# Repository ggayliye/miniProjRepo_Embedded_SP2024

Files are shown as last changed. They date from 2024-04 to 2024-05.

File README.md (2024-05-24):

# Project: Water Storage Tank Refill And Safety Control

Authors: Kyle G. Gayliyev, Hazen R. Brown, Prasanna Umbarkar, Mihir Rane <br>
Date: 29- March - 2024<br>
Course: ECE 6780 - Embedded System Design, ECE Department, The University of Utah<br>
GitHub IDs: ggayliye, Hrb2003, prasannaumbarkar09, patientcoderMR7 <br>
Repo: https://github.com/ggayliye/miniProjRepo_Embedded_SP2024 <br>
Date: By 26-April-2024, 11:59pm (Time of when submission is due/will be ready to be evaluated)<br>
Copyright: ECE 6780, Kyle G. Gayliyev  - This work may not be copied for use in Academic Coursework.

## Overview of the Project
* Pumping water into a container that stops by itself when it's full and fills back again the exact amount when it gets empty. 
* Water fill station that automatically stops dispensing when full, implementation would sense water level without touching it. 
* A small 4V water pump will be connected to the power. The objective is to refill a water container. Once it reaches its high/full level, a signal will be sent to the microcontroller. The microcontroller will interrupt the water pump indicating the water container is full. The same process will take place when it’s empty. The water pump will start working and pump water into the container. 
* The container will include a sensor. This sensor will be placed on the bottom of the container. It’ll sense when the container is “empty” and ready to be refilled. To determine the container’s full state, the water-amount-calculation method will be used: the volume of the container will be known (mL), the speed of the pump for flowing water through a vinyl pipe will be known (x mL/s), and we calculate the amount of time the water pump should be kept on. 
* For the water safety control circuit, we use a MOSFET, an op-amp, an LED, and a speaker. When the water gets salty (adding salt to the water), the alarm will sound along with an LED warning the water is not safe.
* Once the water starts filling the tank, a message is popped on the terminal "Tank empty-water filling in progress" and when completed "tank filled". Also when salt is added toxicity of water can be indicated by "toxic water" on the terminal. This is all done by UART.
* The water safety implementation will only be based on chemicals that are ionic and/or electroconductive. Specifically, we will focus on Sodium chloride (NaCl) in our testing. This means that the “unsafe” measurement will be sensitive to salt. 
* The technical implementation of the “unsafe water” indicator is going to be in the container. It’s planned to be a simple design: installing an active power probs inside the container. When water hosts polluting electroconductive elements, it will create a path to transfer electrons that will trigger the measuring sensor. The power source will be set very low; it will be very safe to use. 
* This project has applications in drinking water storage tanks, petroleum refineries, and more. 
* Our design will be very safe to use as we take all precautions and safety measurements before the launch.
* In this project, we implemented interrupt, GPIO, UART, and motor drive.
* For the software, we used C programming language and coded using Keil uVision5.

## List of Materials : 

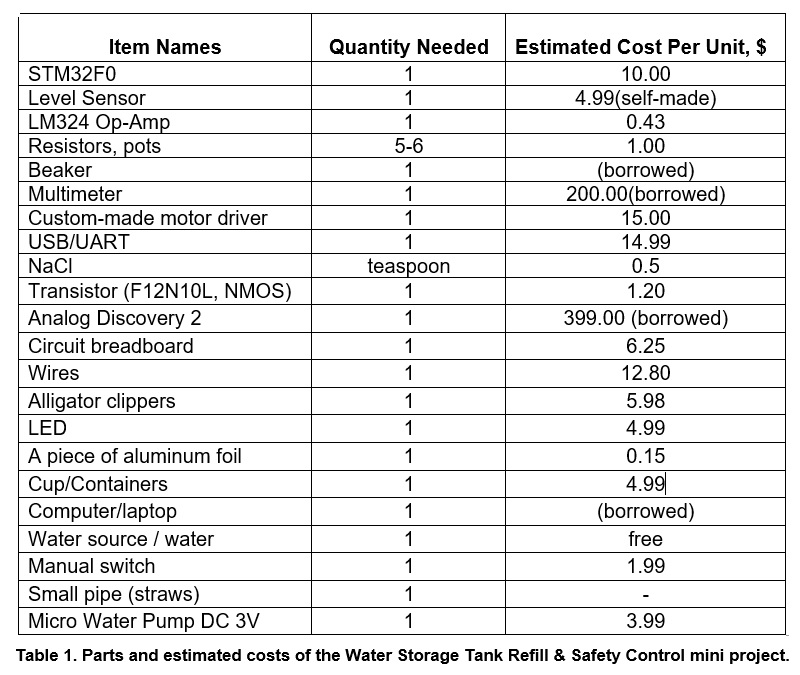
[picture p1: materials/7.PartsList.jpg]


## Functional Block Diagram of The Project: 

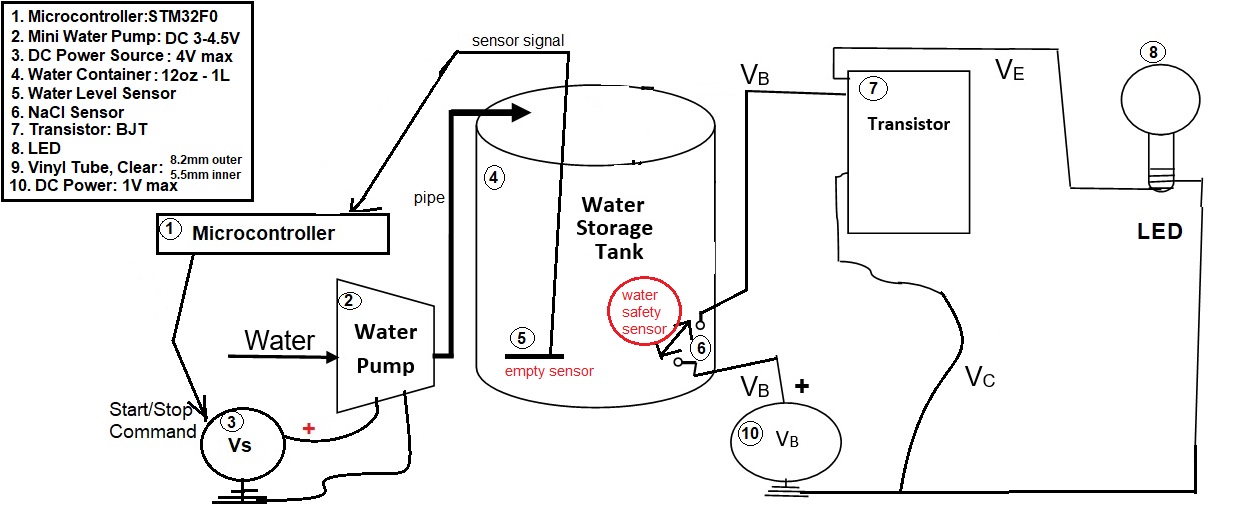
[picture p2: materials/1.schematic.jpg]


## Schematic of The Project: 

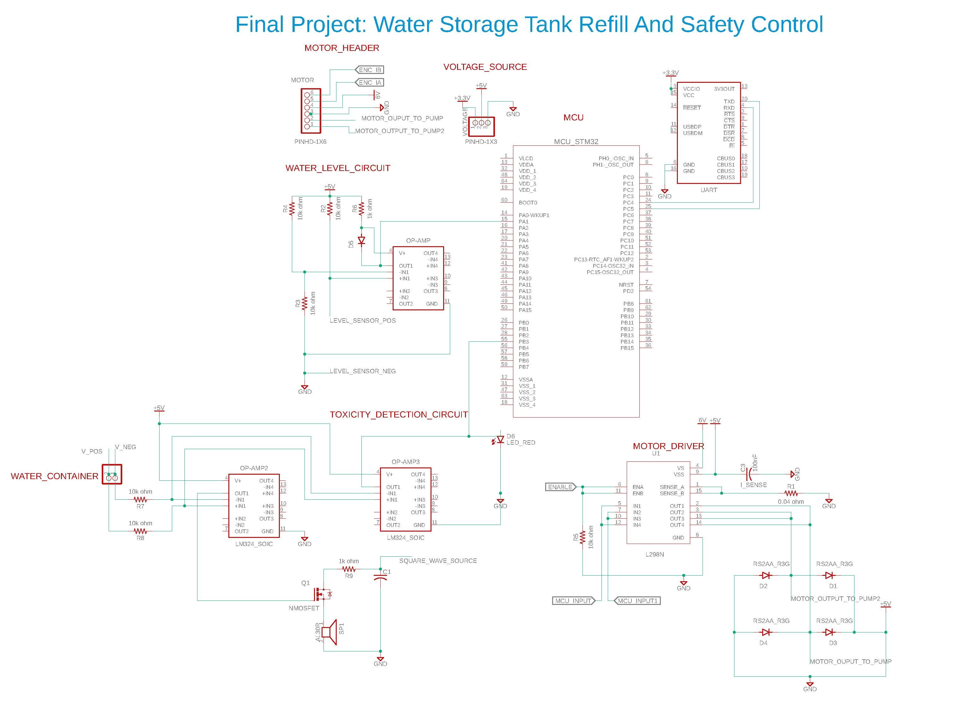
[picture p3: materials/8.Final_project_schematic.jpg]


## A List of 4 Implementation Milestones:

- Due by March 5th :  Determine the sensors.
- Due on April 12th:  Microcontroller code is ready and working.
- Due on April 19th:  Demonstration of a passing test with all components installed.
- Due on April 26th : Final Delivery.

### Some of the projected tasks to do:
* Develop code to effectively operate the water pump.
* Develop code to collect data from both sensors.
* Assemble the dispenser and integrate the water pump code with the sensor code.
* Test and fine-tune the device for practical functionality.

## Risks Associated With The Project And Plans To Compensate:

The use of water near electronics will require extra protection/care of the devices and connections. Additionally, the use of an ultrasonic sensor to measure the height of water may be difficult and could require extra work to ensure correct functionality. The most challenging part is expected to be implementing the water level sensor.

<pre><ins>Future extensions</ins> : This mini-project is about a month-long project. Each week, we'll meet with a TA 
to discuss the progress of the project and update the TA about the project's situation. As a group, 
we'll be continuously working on this project updating it each week. It'll be finished at the end 
of the semester whether we accomplish our goals or not in this project. </pre>

# Partnership

This project is worked on as a requirement of the "ECE 6780 Embedded System Design" class at the ECE Department at the University of Utah. The class requirements demand this project to be done as a group of a minimum of three, and a maximum of four students. The group members for this project are listed on top of this page in the header. Most of the work is expected to be completed collectively/in groups in this project and not like the "divide by task" style. A very limited amount of tasks will be assigned to group members as individual work/divided work.

# Progress Notes

<ins>1st Week Notes:</ins> <br>

By March 13th

- The project proposal is submitted.
- Feedback is received from the TA about our project proposal.<br>

<ins>2nd Week Notes:</ins> <br>
By March 22nd:

- The project GitHub account is created.
- All members added to the repo and members practised "commit" action.

<ins>3rd Week Notes:</ins> <br>
By March 29th:

 <pre>Mini-Project Milestone 1 :  </pre>

This week on Thursday, we met with Ashton during office hours and discussed our project's status.<br>

We talked about the implementation of the microcontroller, the motor's pumping speed, and water level sensors. As we mentioned in our project proposal, we're expecting the water level sensor to be the difficult part of the project.<br>

We updated the TA on what we have done and talked about our team meeting in the week. We determined the tasks we planned to do in this week's experiment. <br>

Today on Friday, we met with the team to test our motor, microcontroller, and measure the speed of the pump. <br>

In our group meeting today, we measured the speed of the pump. We found the running current of the motor to be 170 mA. The other experiment results with the water pump are below:

1. *138 mL of water is filled in 4.75 sec.*
 
2. *100ml of water is filled in 4.58 sec.*
 
3. *100mL of water is filled in 5.92 sec.*
 
4. *100ml of water is filled in 5.35 sec.*
 
5. *100ml of water is filled in 6.17 sec.*
 
Avg: 5.505 sec for 100ml.<br>

- We will be testing the completed section of the project each week. Before the final week, we'll be testing the project with all components together. In the final week, we'll also demonstrate the project's function as a whole.

Pictures from the experiment day: <br><br>
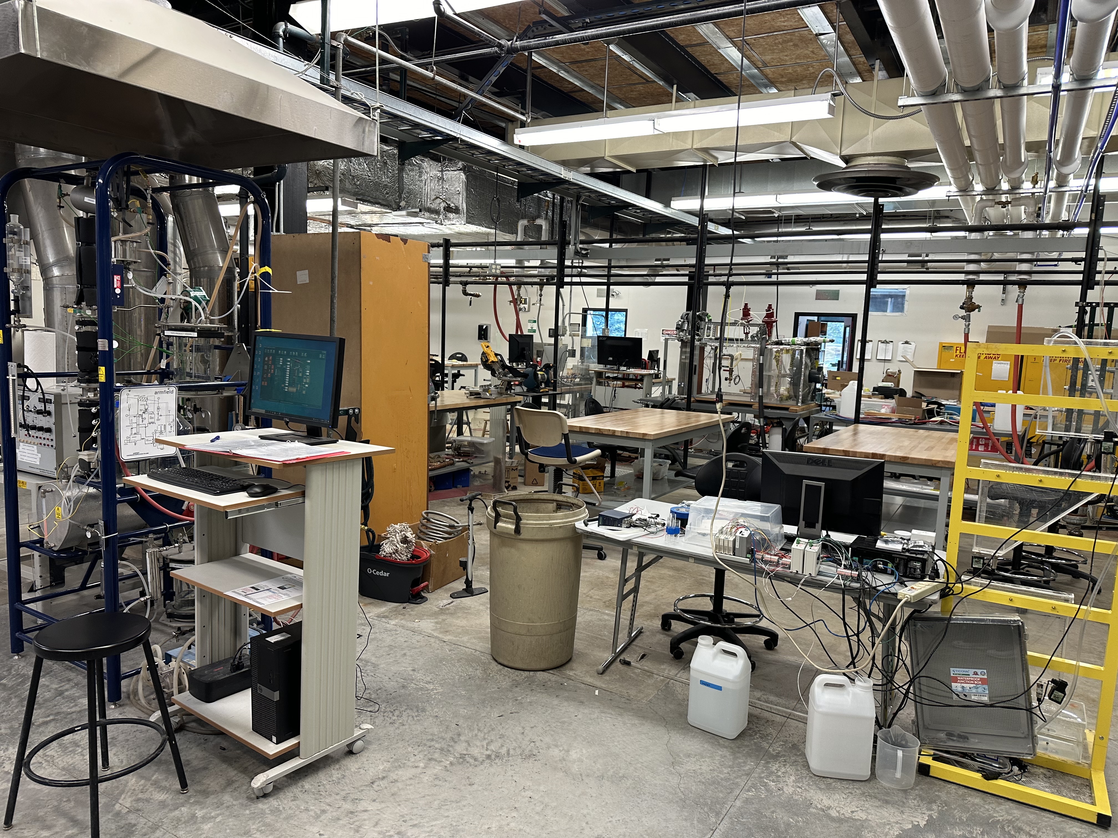
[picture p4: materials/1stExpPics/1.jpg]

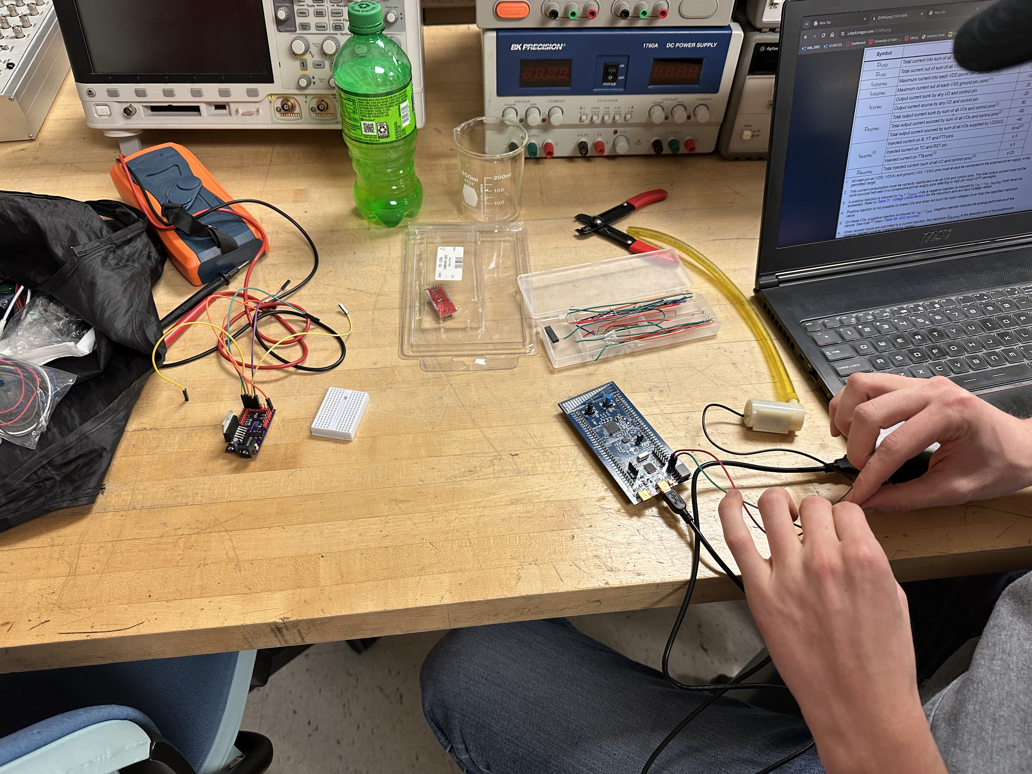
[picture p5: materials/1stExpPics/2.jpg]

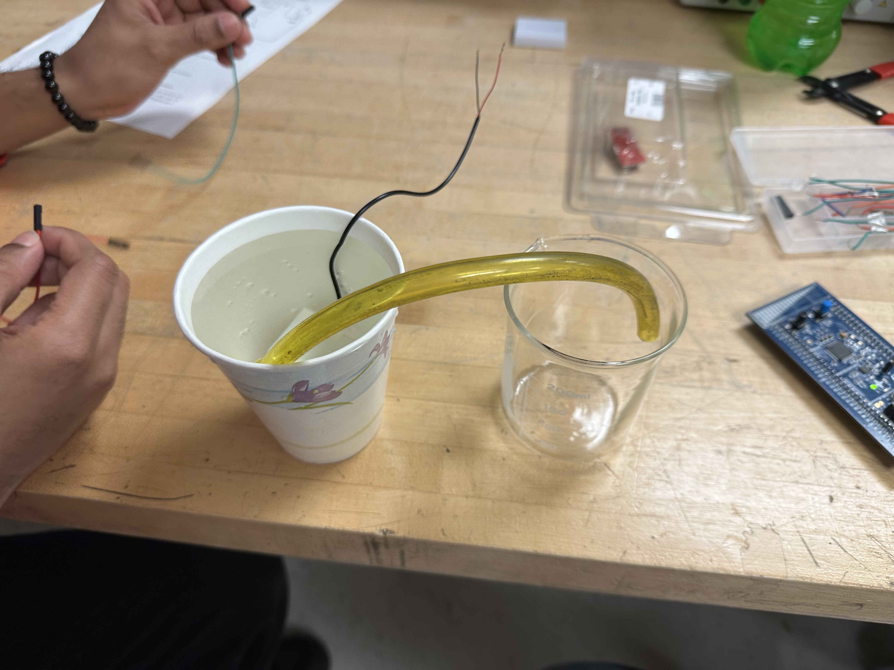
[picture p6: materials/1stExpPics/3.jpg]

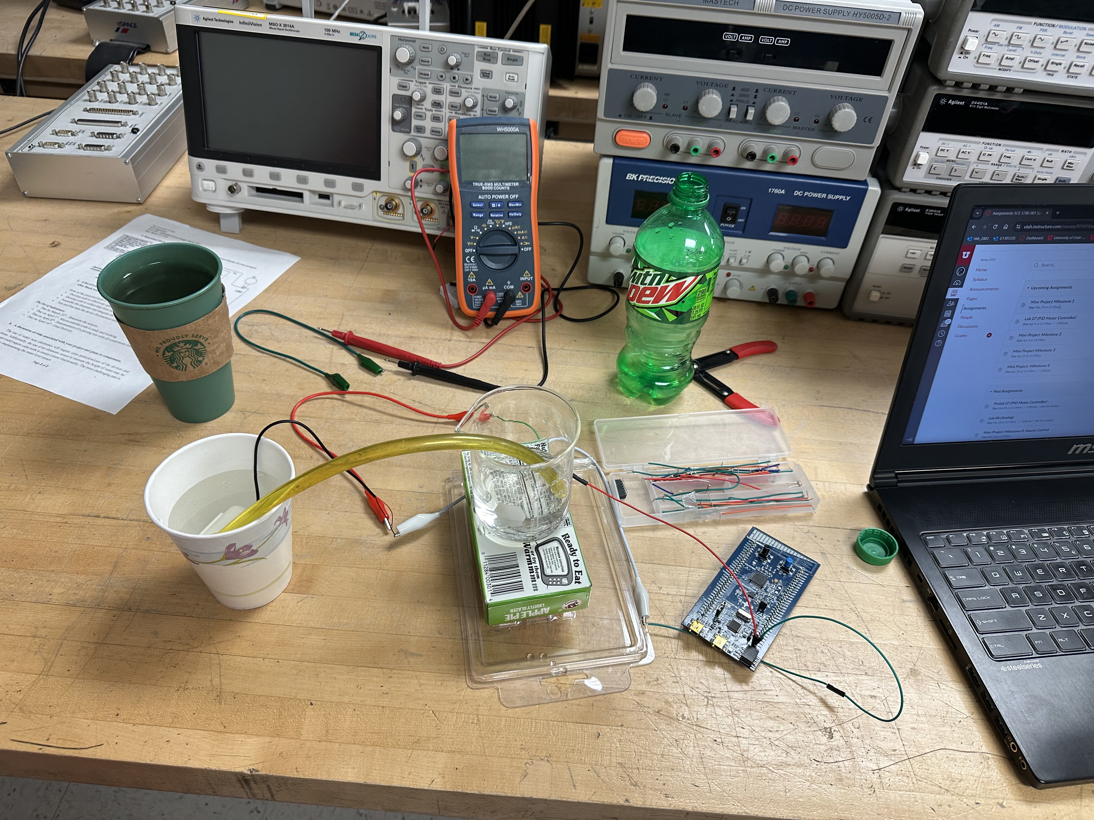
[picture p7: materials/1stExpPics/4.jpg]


<ins>4th Week Notes:</ins> <br>
By April 5th:
<pre> Mini-Project Milestone 2 :</pre><br>

- This week on Friday, we met with TA Baily in the morning lab hours and discussed our project's status.

- We talked about the implementation of the microcontroller and a water-level sensor prototype.  We tested an LM324 comparator and metal probes to sense the water level. We successfully were able to trigger the interrupt that signals when the water storage tank is empty (water level). 

- After the lab, we met to do the sensor-level testing and the comparator implementation.  Also, we were able to send the interrupt signal to the microcontroller to be able to read the signal and respond as an interrupt. The L292, from our soldering PCB assignment, is used to run the motor and change the motor speed adjusting PWM.

- The water pump motor is driven at 4V allowing modulation (PWM) between 80% and 100%.

- We foresee our working motor speed may change when we progress on this project.

Pictures from the Milestone 2 experiment day: <br><br>
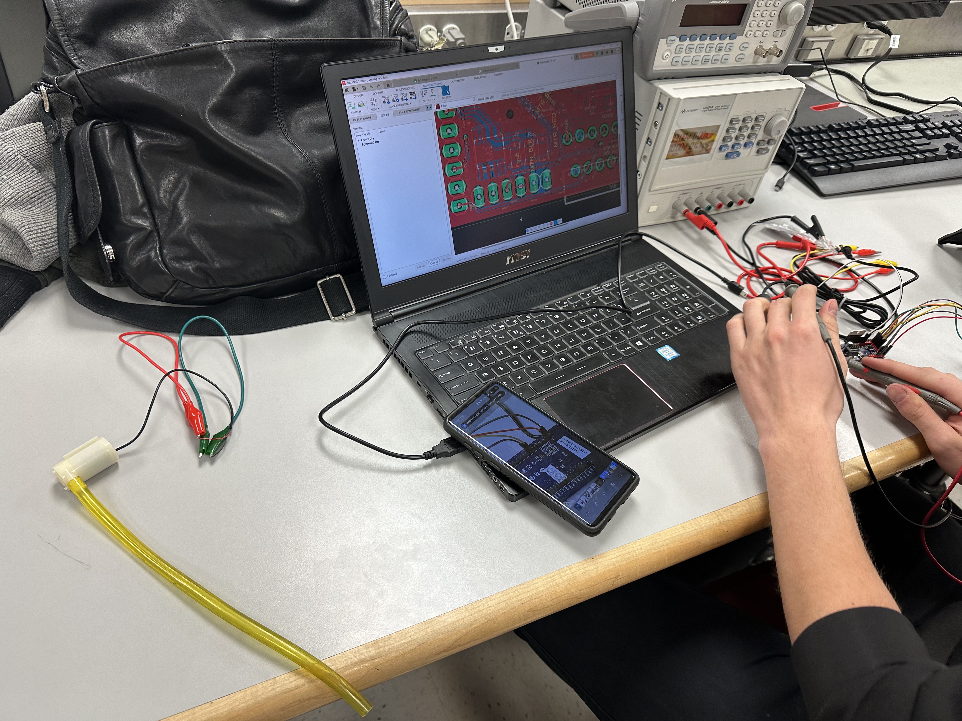
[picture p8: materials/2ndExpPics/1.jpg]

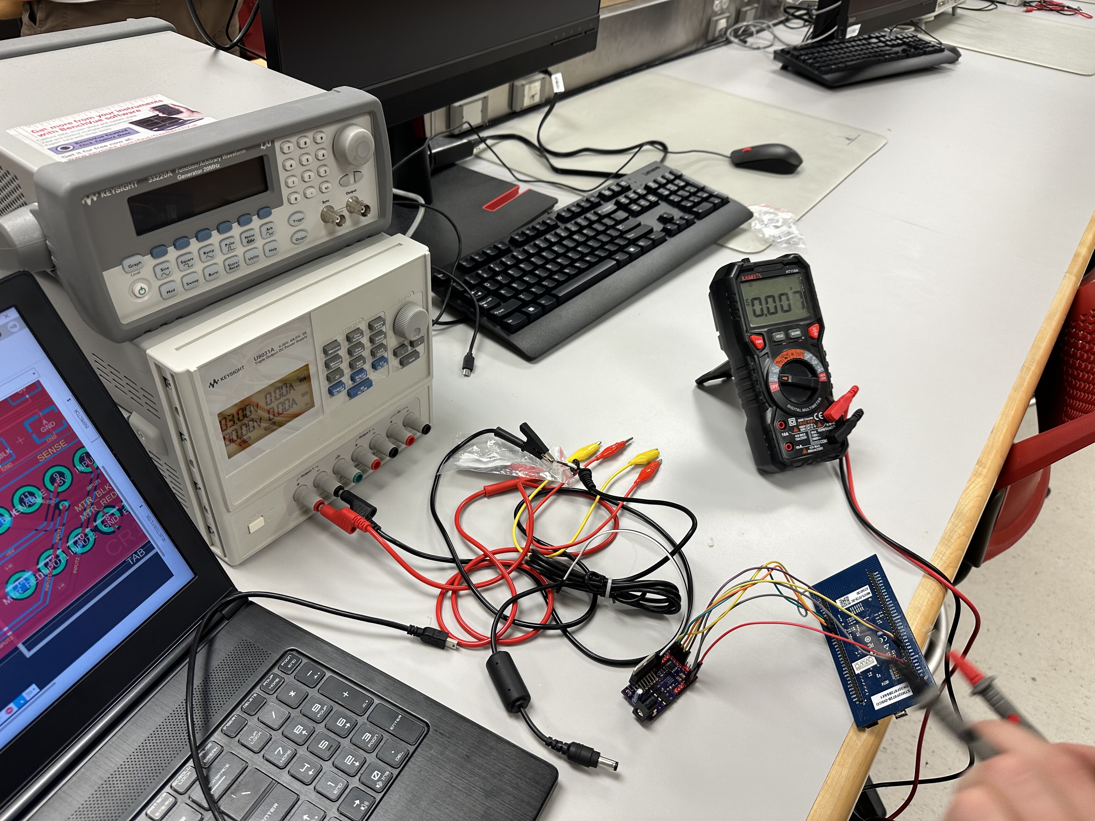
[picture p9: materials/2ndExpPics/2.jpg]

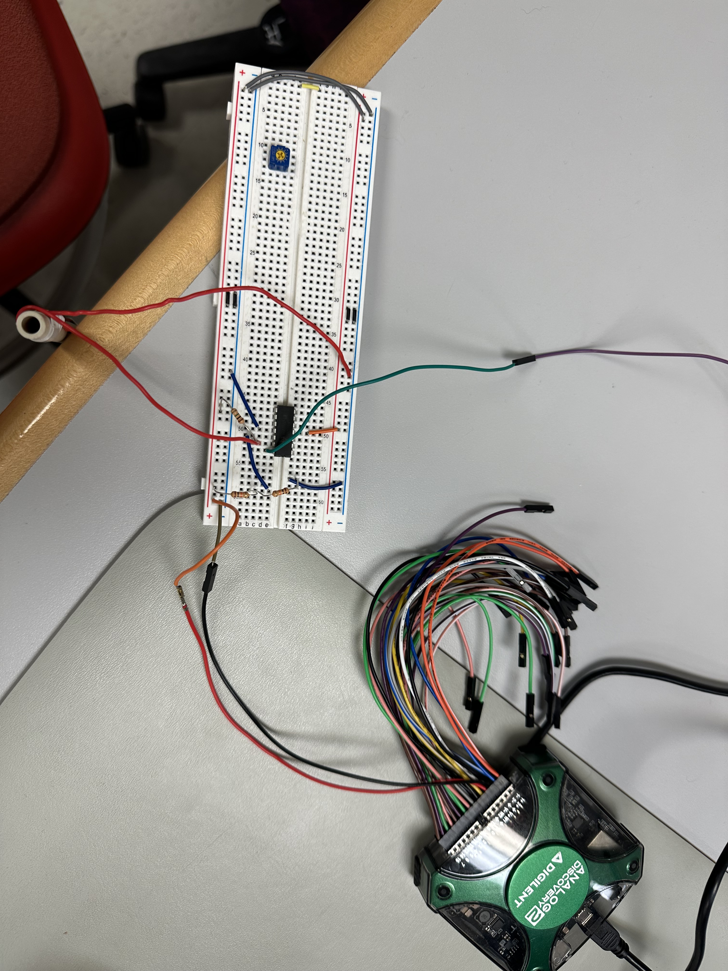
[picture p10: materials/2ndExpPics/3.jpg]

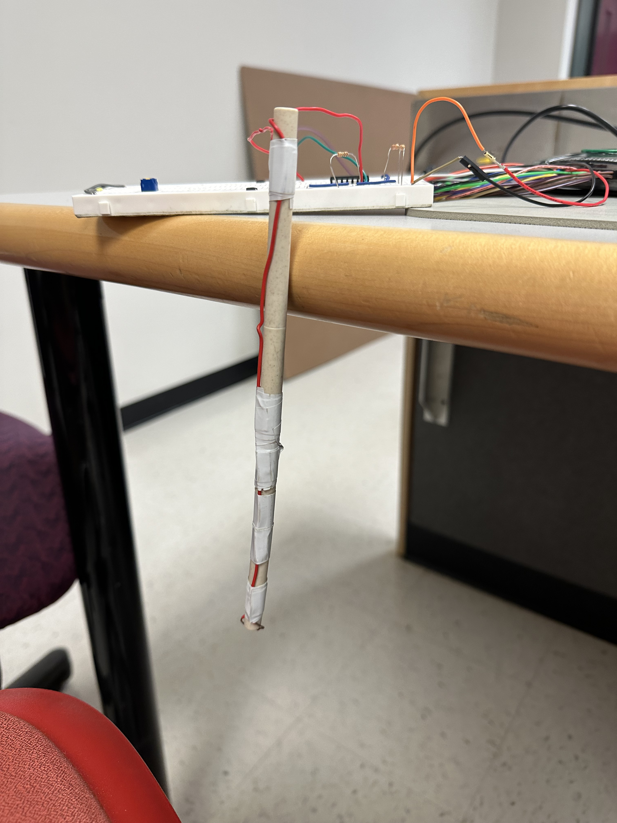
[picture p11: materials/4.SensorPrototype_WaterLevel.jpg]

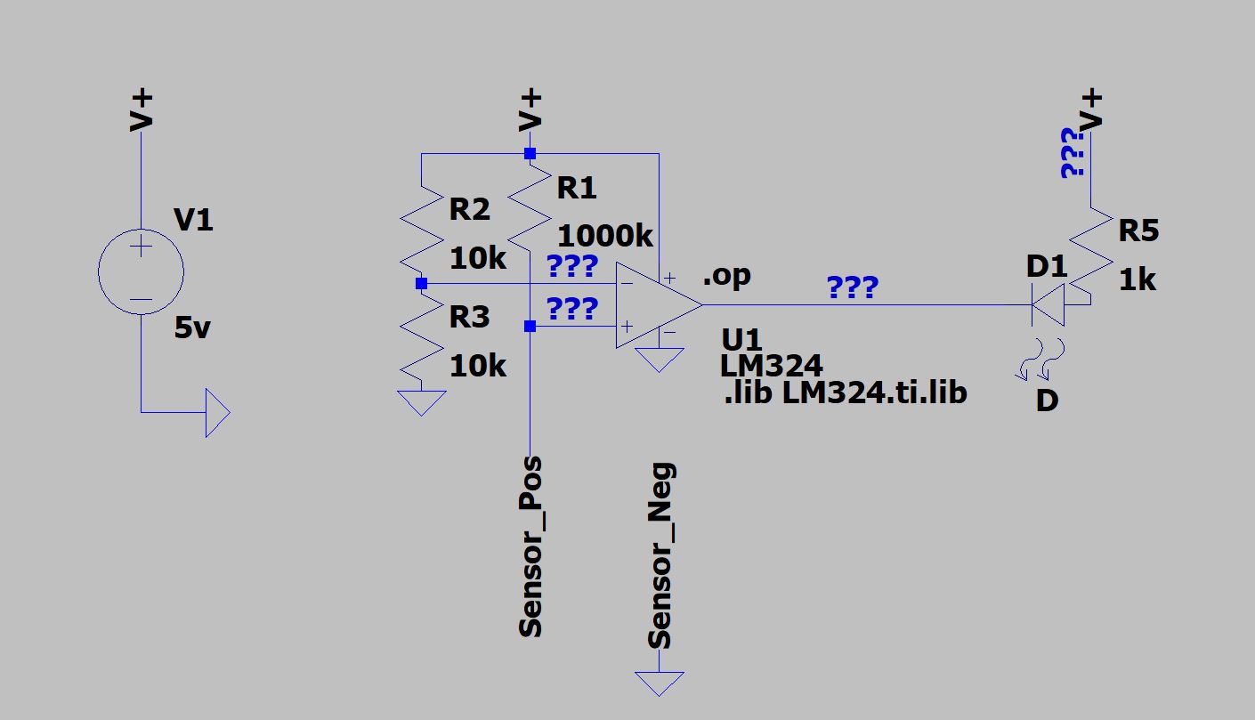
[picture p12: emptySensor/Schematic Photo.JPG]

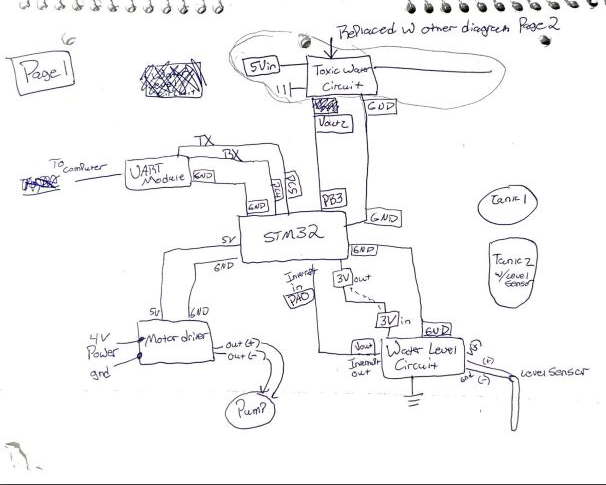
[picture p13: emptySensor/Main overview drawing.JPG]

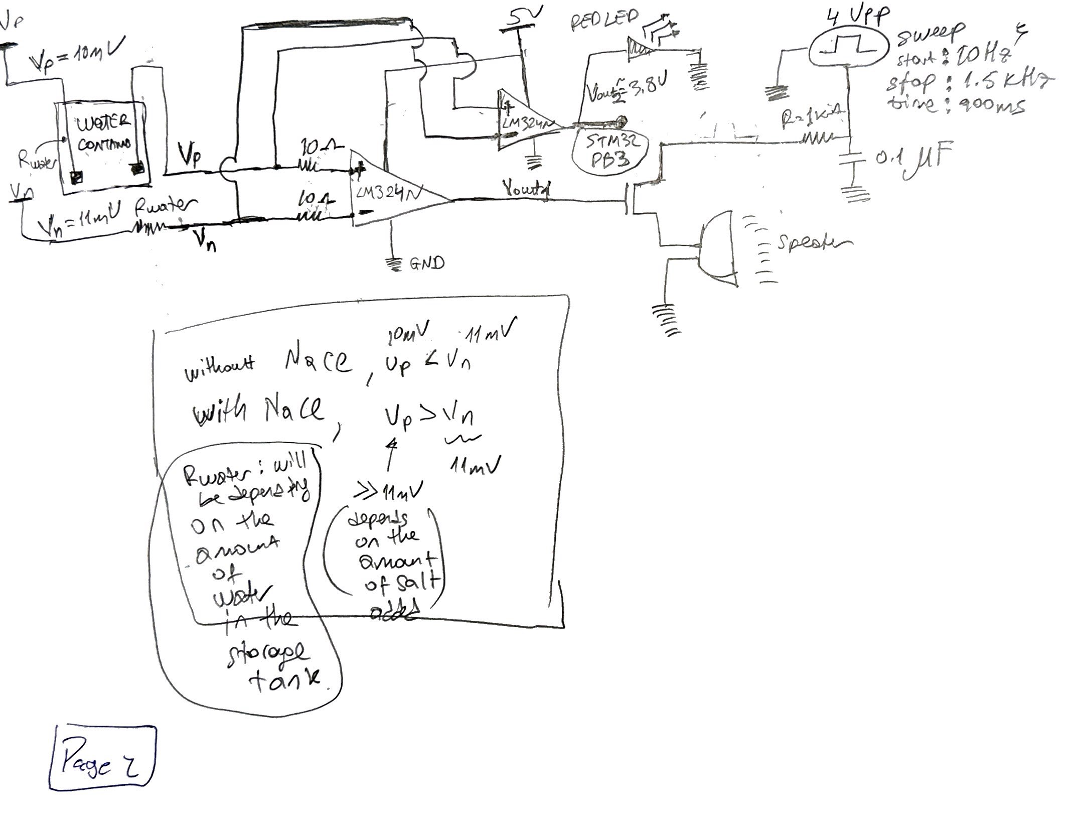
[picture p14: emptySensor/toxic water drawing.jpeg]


<ins>5th Week Notes:</ins> <br>
<pre> Mini-Project Milestone 3 : </pre><br>

- On Friday during our lab time on the 12th of April, we gathered with all team members to progress our project one step further. In our meeting, we implemented the sensor signal-microcontroller interface and UART-microcontroller interface.

- At the beginning of the project, we had predicted the most challenging part would have been implementing the water level sensor. This sensor implementation was expected to be challenging because it should sense the empty status of the water container. However, it's good news that we were able to successfully implement it during our lab meeting this week.

- To give a little bit of background information on how the empty tank sensing should work is that we implemented the physical sensor on the bottom of the water tank wired with a microcontroller connection. When the water level reaches low, the sensor sends an analog signal to an op-amp that works as a comparator. It compares the Vp and Vn input pins and outputs Vcc in the Vout that is connected to the microcontroller. When the analog signal is received from the op-amp, which will signal that the container is empty, the microcontroller will turn the water pump on, and the pump starts refilling the water container. The microcontroller will interrupt in the end when the container is full and that will indicate the time to stop pumping water.

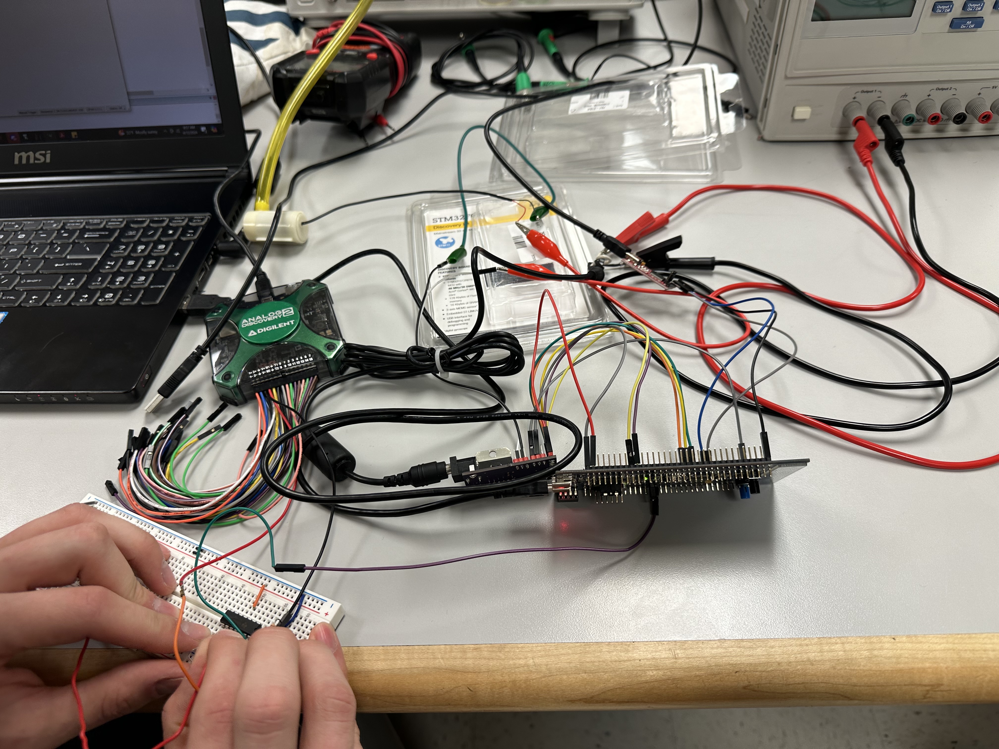
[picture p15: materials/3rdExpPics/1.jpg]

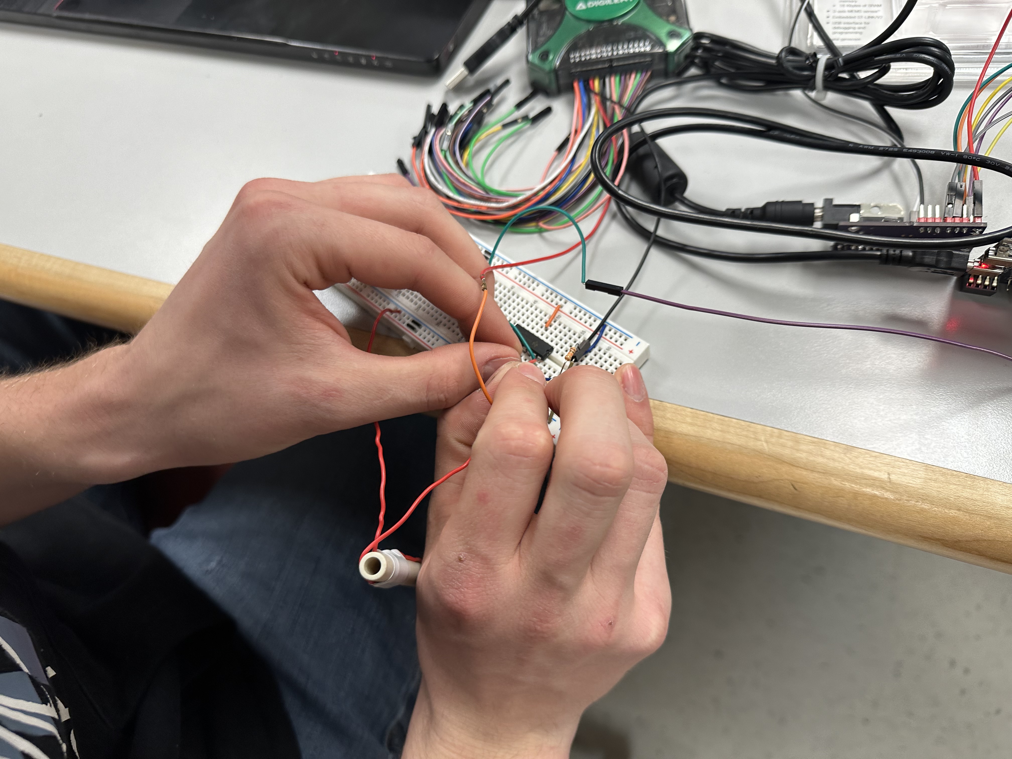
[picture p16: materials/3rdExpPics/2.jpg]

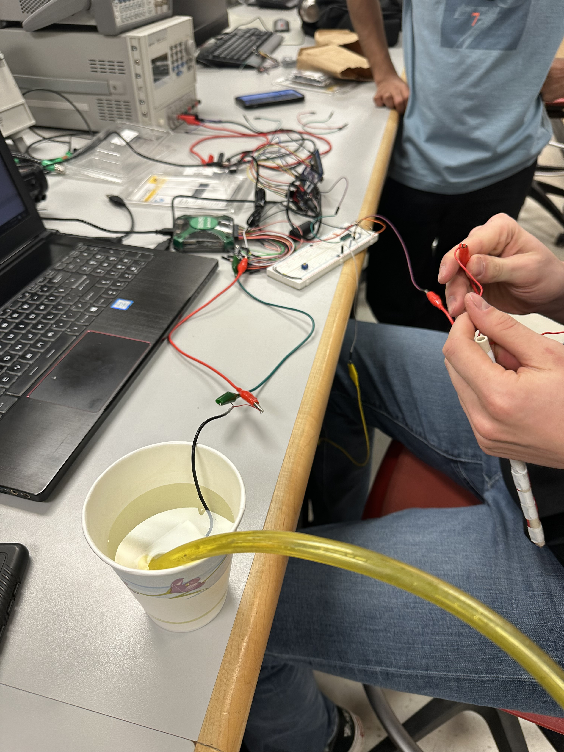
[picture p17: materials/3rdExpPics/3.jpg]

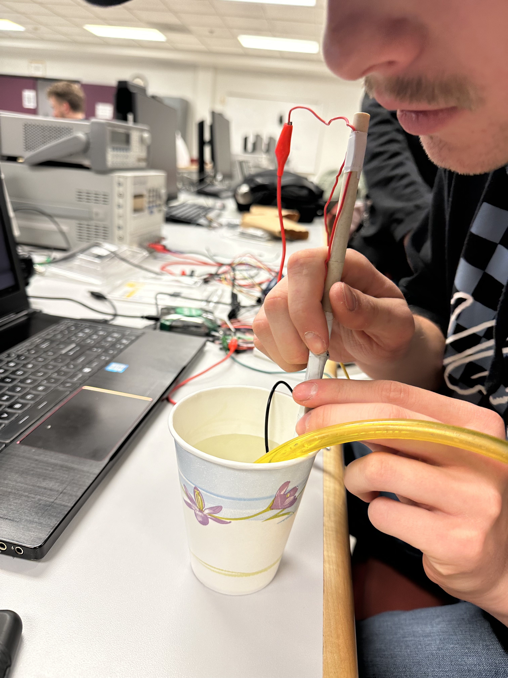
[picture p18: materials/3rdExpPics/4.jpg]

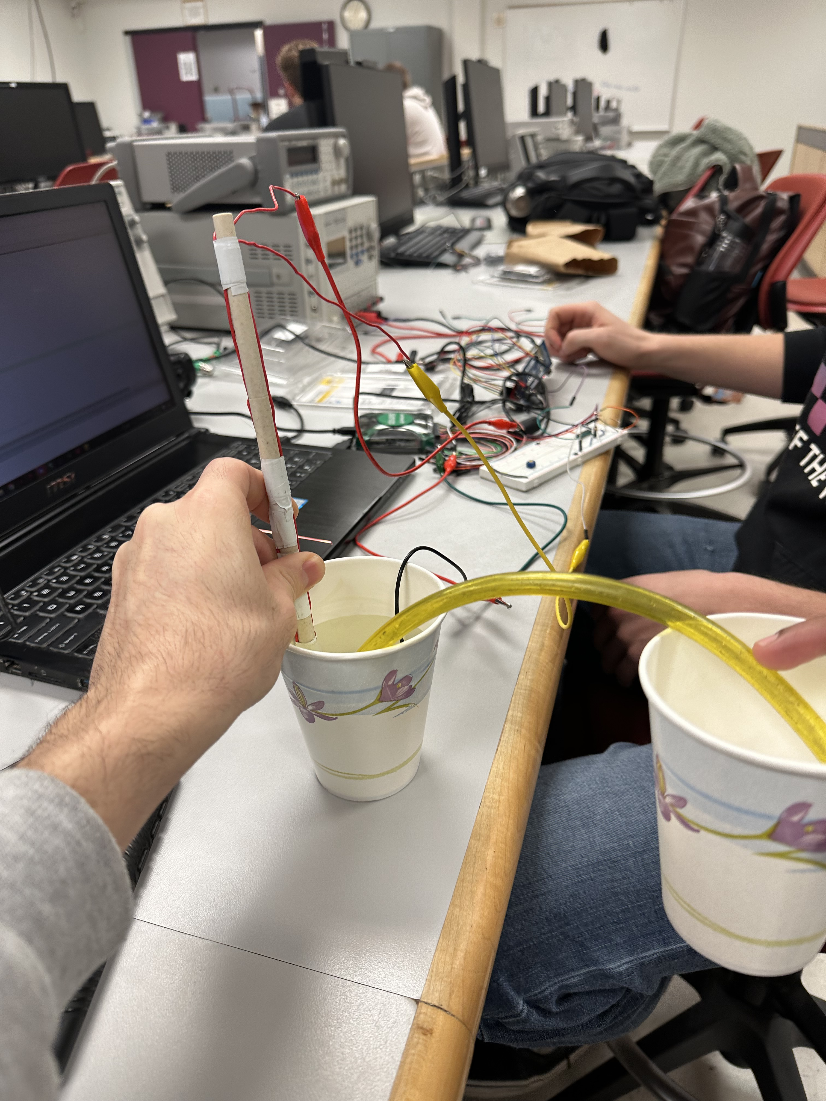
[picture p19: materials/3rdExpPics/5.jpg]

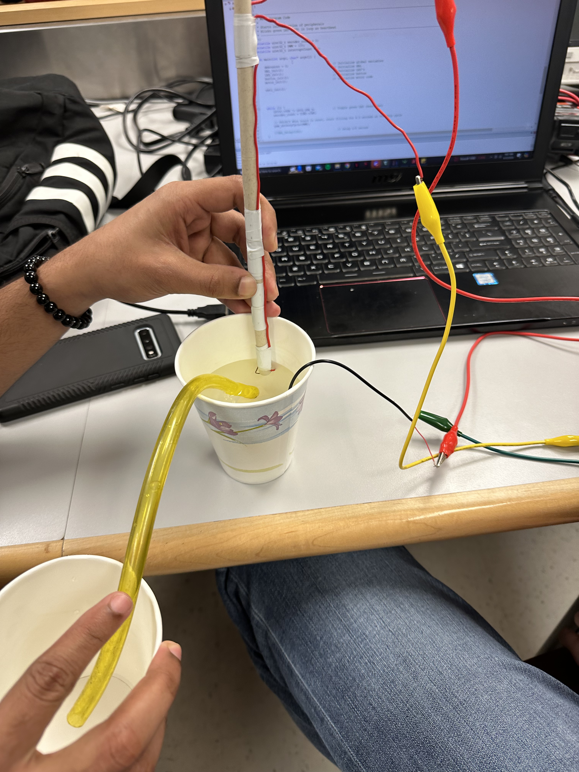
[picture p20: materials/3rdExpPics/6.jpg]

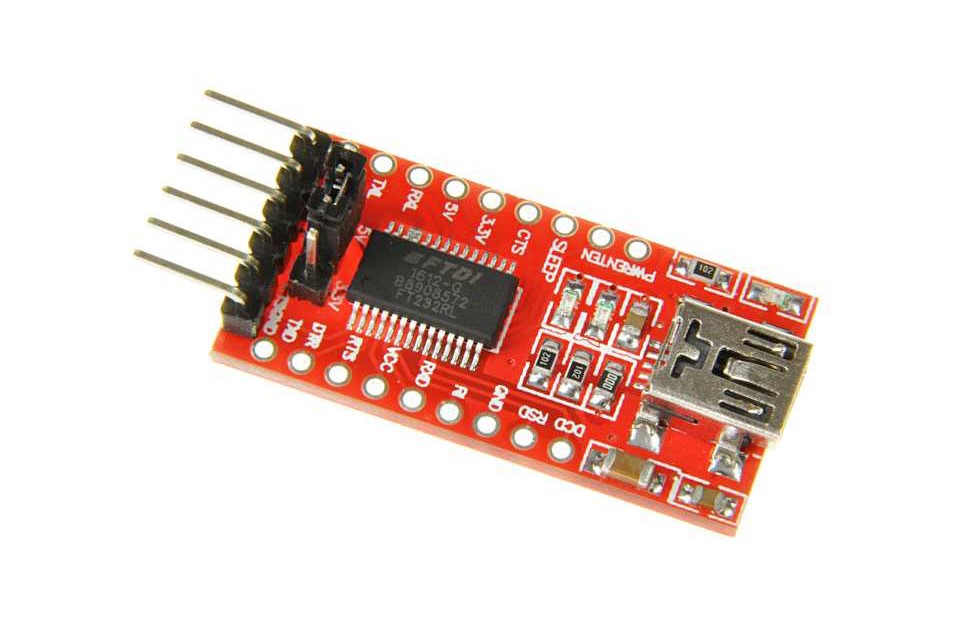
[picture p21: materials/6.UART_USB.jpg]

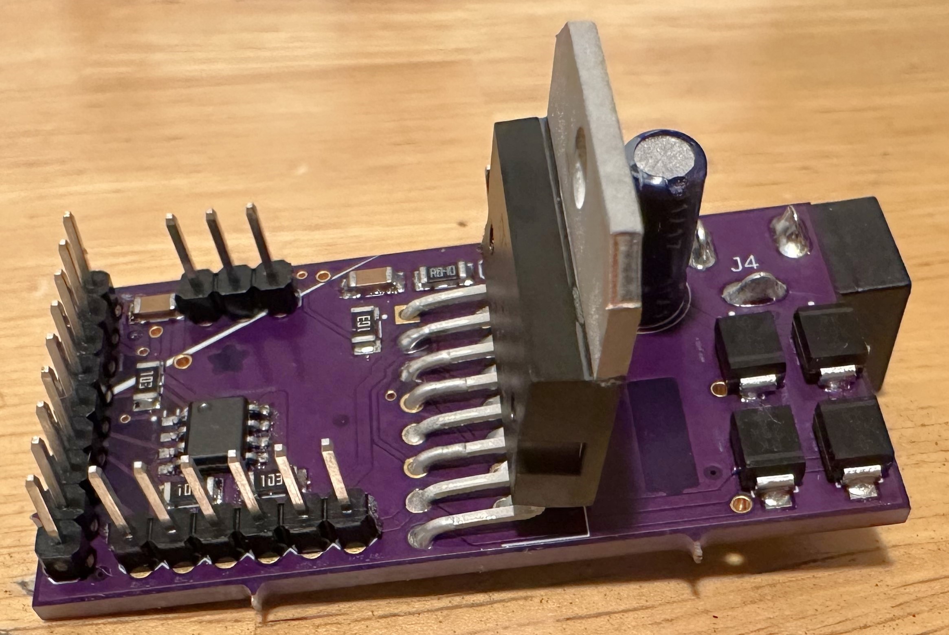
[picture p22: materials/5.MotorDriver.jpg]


<ins>6th Week Notes:</ins> <br>
<pre> Mini-Project Milestone 4 Final submission : </pre><br>
- Today, on April 24th, we meet up to complete our project in the lab. We successfully implemented toxicity detection, as well as water level detection with UART messages displayed in the terminal.
- Our project implemented water storage tank refill and safety control. In our previous milestones, we had implemented water pump control using a motor driver we created and soldered in one of our class lab assignments, microcontroller, UART transmit and receive interface, and GPIO LED implementation. 
- The project implementation starts when the water storage tank is full. Today during our lab tests, first, we drained water and checked the water level sensor's response.
- The water level sensor is set close to the bottom of the tank. When the tank was fairly empty, we verified that the microcontroller gave a start to the pump.
- The water pump kept running while pumping water until the water storage tank was refilled. It was interrupted by the microcontroller stopping the pump when the water level reached full. 
- Second, we tested the safety control of the water container. As we mentioned before, we did this test with NaCl(salt). 
- After setting up the experiment equipment, we poured some salt into the container. Our circuit implements safety control triggered by the salt added into the water alarming by a speaker and making an LED on.
- The alarm system is built using an op-amp and an NMOS. The NMOS transistor works as a switch allowing a square wave set up as a sweep flowing from drain to source.
- Additionally, our system allows for manual control of the pump over UART. A user can turn the pump on and off, as well as change between three preset pump rates. The microcontroller will automatically send messages to the terminal when the tank is empty, or full, or if the water has gone toxic. 
- Overall, we completed all milestones and tasks for this mini-project that were initially set.

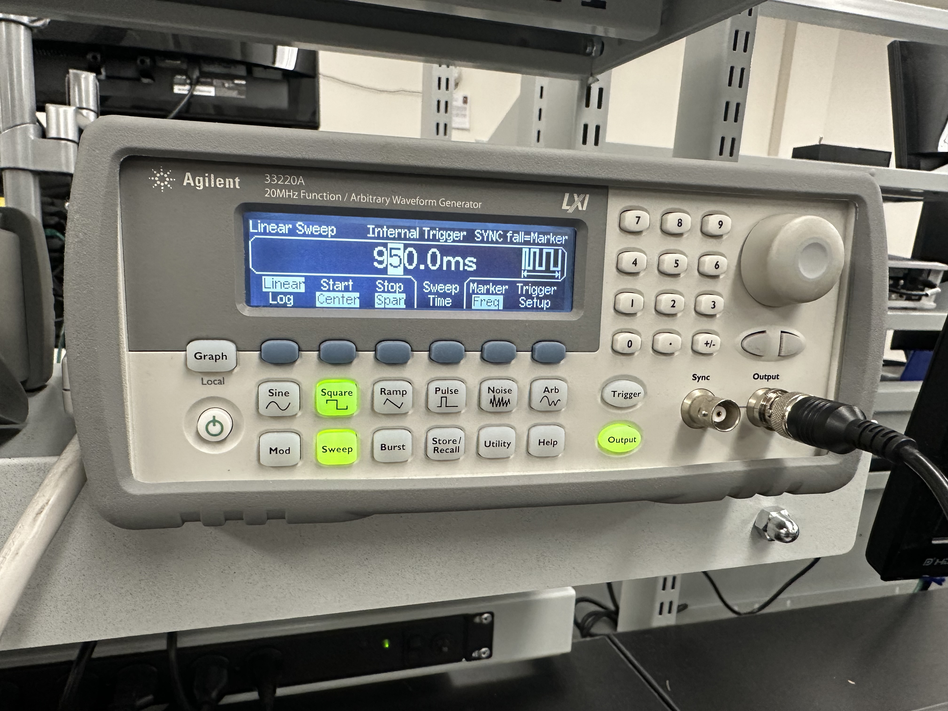
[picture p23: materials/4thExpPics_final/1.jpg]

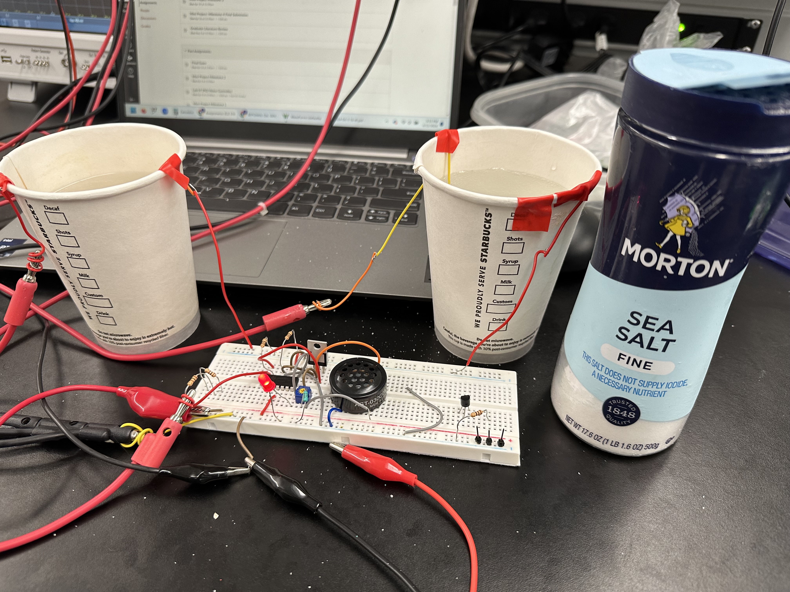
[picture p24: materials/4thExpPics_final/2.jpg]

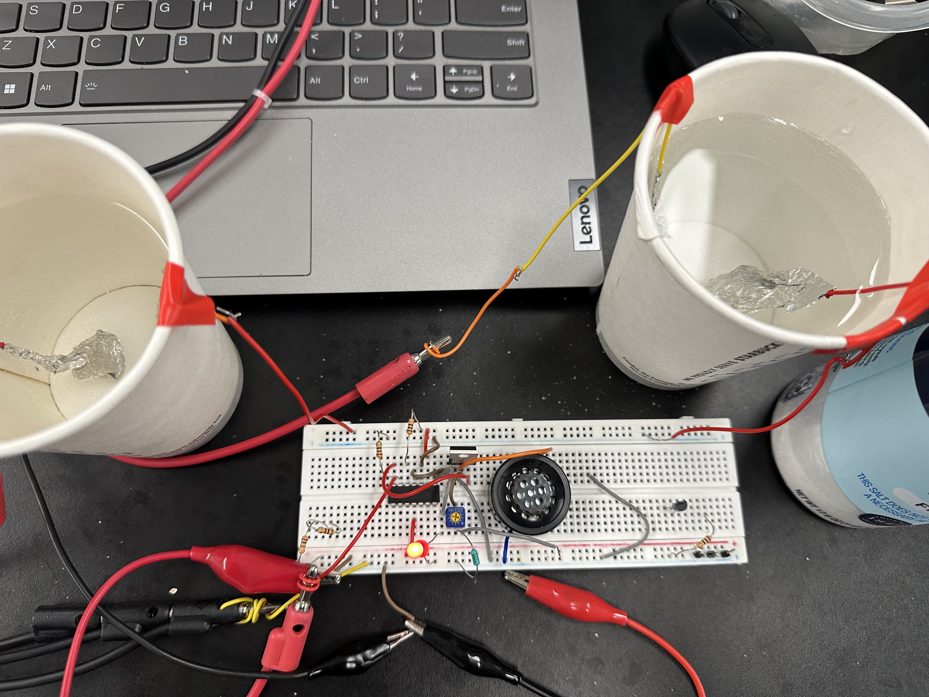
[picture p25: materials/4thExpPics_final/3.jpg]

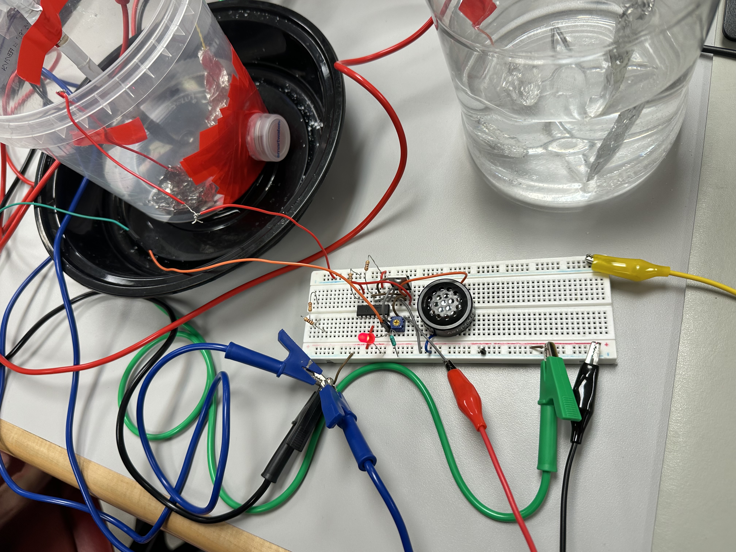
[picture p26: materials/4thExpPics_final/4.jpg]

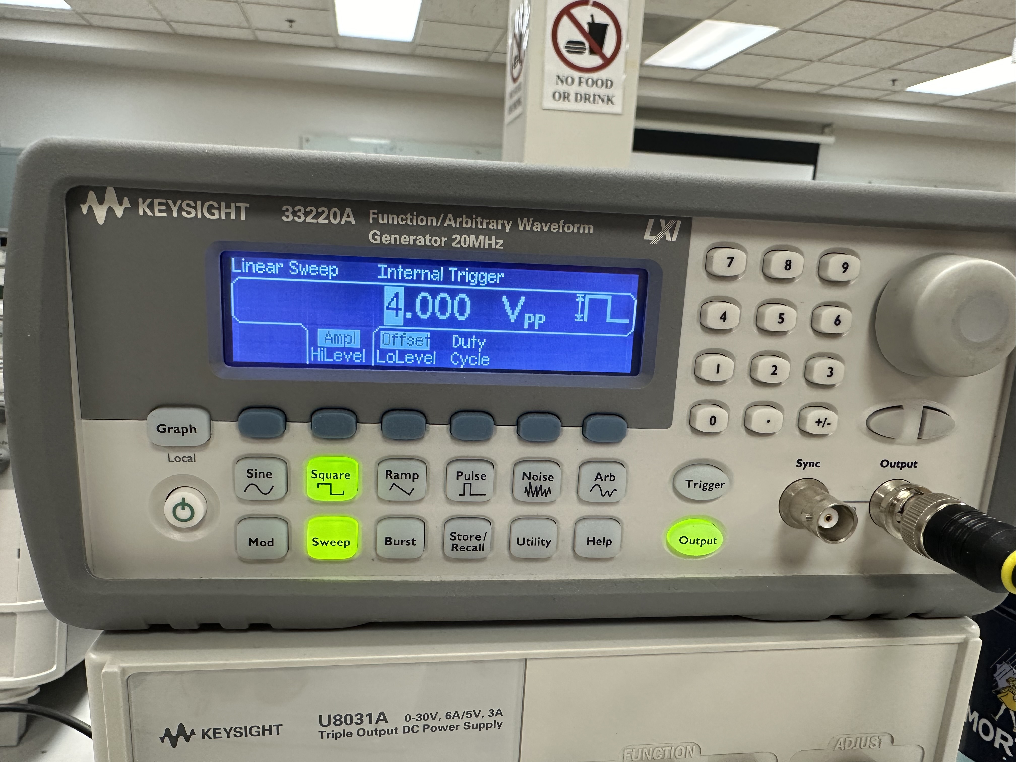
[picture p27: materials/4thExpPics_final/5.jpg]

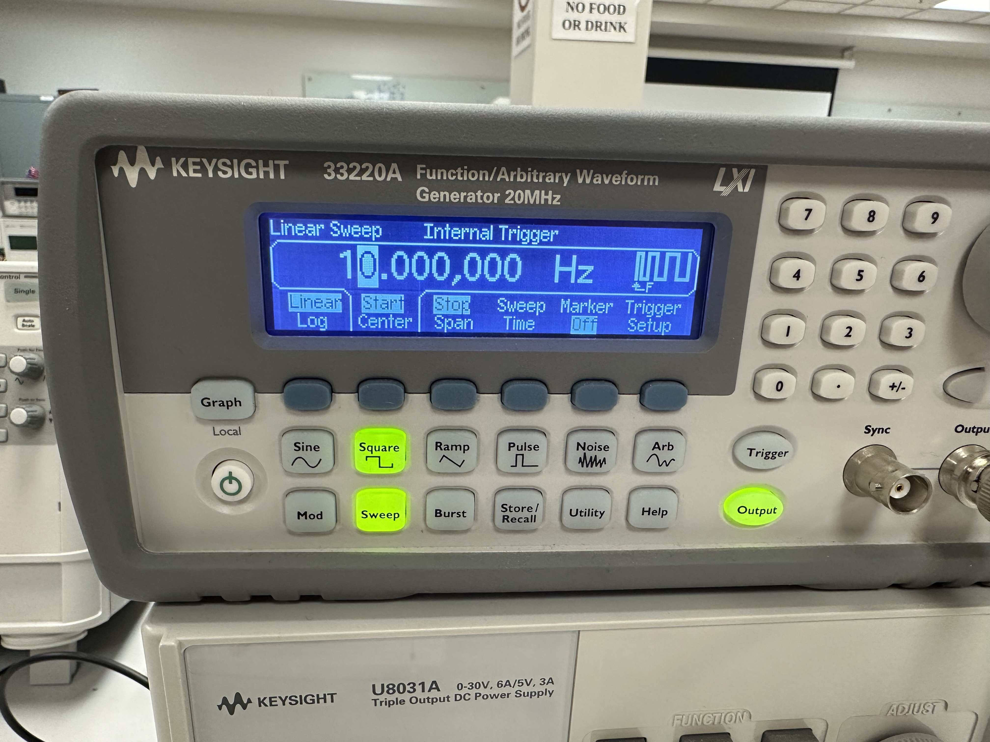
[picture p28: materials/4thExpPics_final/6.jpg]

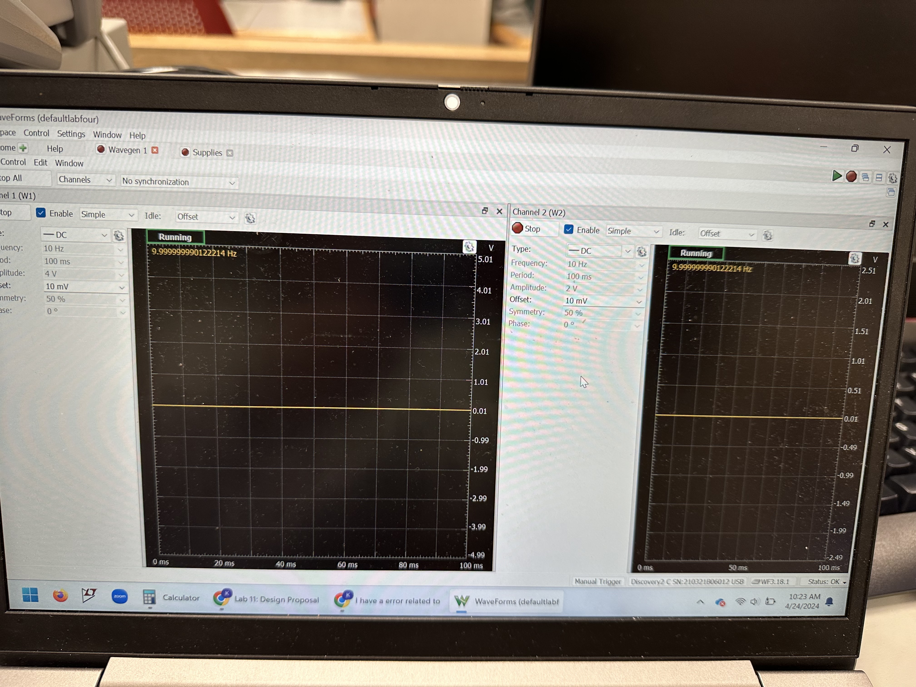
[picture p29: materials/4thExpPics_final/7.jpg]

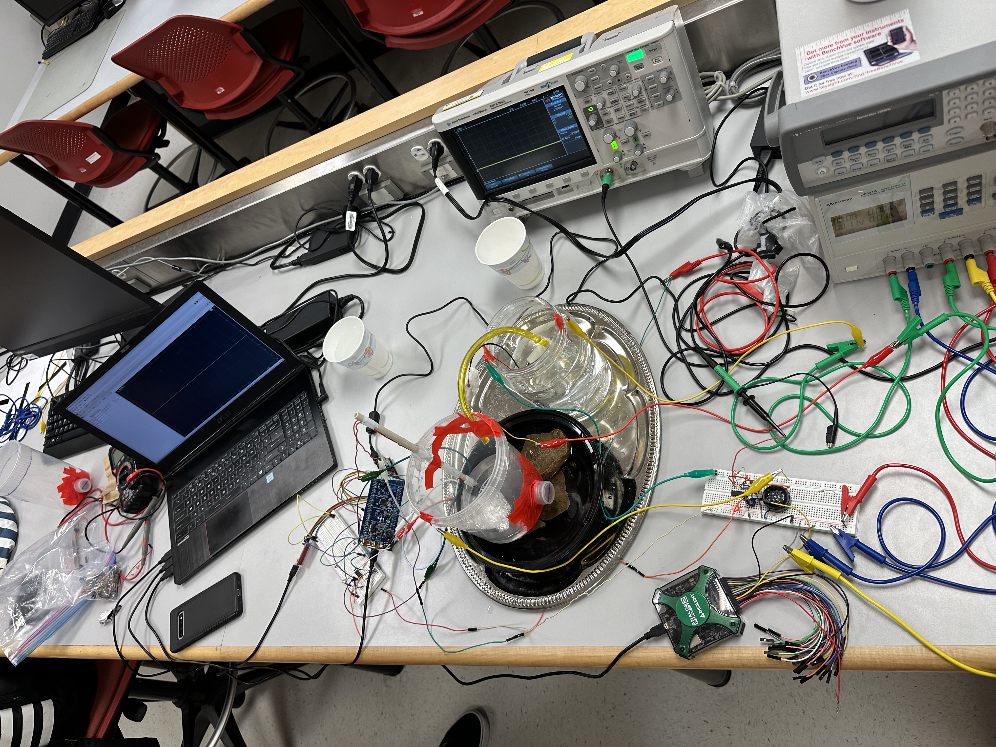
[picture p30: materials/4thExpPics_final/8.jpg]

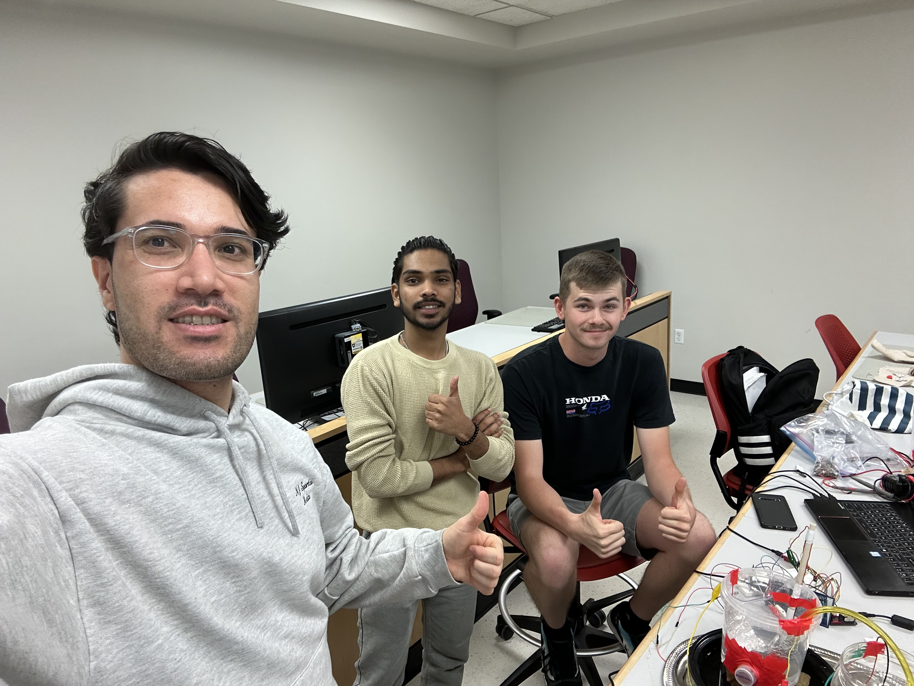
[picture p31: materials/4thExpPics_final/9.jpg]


# Time Expenditures:
<pre>Predicted Hours: 15h		Actual Hours:	16h		 </pre>

The actual hours recorded on top reflect the time spent on the mini-project including the time spent in labs for experiments. It excludes time spent reading, researching, and understanding the contexts or materials that are required to complete the tasks related to the project.

# Comments to Evaluators:

Thank you for evaluating this project and providing feedback. <br>

Have a wonderful day!

# Testing

- The water storage tank should be at a higher level than the water container that water is pumped from. Otherwise, the water transfer will occur until both containers' levels are balanced with the help of gravity without the pump.

## Project Testing Set Up

- Two water containers are needed: one of them to be filled with water and the other with just enough water to cover the level sensor. 
- The water level sensor is constructed from two copper wires taped to an insulating rod. These wires attach to the water level comparing circuit which sends a high or low signal to the microcontroller. 
- To measure toxicity, both containers should host a wire to allow current to flow through the water. This will measure the resistance of the water, ensure equal residency in case pH (potentially may change between 0-14) changes, and compare the "standard" water sample to the "tested" container by sending the signals to the LM324 op-amp's Vp and Vn pins. Depending on the safety, the op-amp will have 2 distinct outputs that help trigger the safety alarm if NaCl is detected.
- This op-amp's output should go to an NMOS transistor gate. The NMOS transistor's drain receives a square wave with a sweep from 10 Hz to 1.5 kHz. The sweep time should be set to 900ms. The amplitude should be set to 4 Vpp. On the source of the NMOS, a speaker is connected. The speaker's other end is connected to the Ground. 
- The op-amp receives 5V in DC on the +Vdd and 0V/Ground on the -Vdd.
- When the water contains enough salt to be determined unsafe, the comparator triggers the rest of the toxicity circuit to sound the alarm and illuminate the LED. This toxicity circuit also sends a high or low signal to the microcontroller. 
- The low-level circuit output signal is connected to pin PA0 of the STM32, and the toxic water circuit output signal is connected to PB3 of the STM32. These signals trigger interrupts within the microcontrollers software which allow for enabling and disabling the pump. 
- The water pump is connected to the motor driver. We are driving the motor at 4V so we supply the motor diver with a constant 4V DC supply. 
- For full USART capability, PUTTY or any other UART terminal is required. 
- To test the system, water can be drained from the water tank. Draining the tank below the set threshold will automatically trigger the motor to turn on and begin refilling the container. When the pump kicks on, a message will be transmitted over UART signaling the pump is running. The pump will then pump for a preset time until the water tank is full, once again signaling over UART that the tank is full.
- In the case a user wishes to change the pump rate, or manually enable/disable the pump, these commands can be sent over UART. Pressing M followed by 1 in the terminal will turn the pump on, and M - 0 will turn the pump off. To select various pump speeds, the commands A - 0, A - 1, and A - 2 can be used. 0 commands 100% PWM, the "1" commands 95%, and "2" commands 90%. 
- To test the water toxicity circuit, salt can be added to a full water tank. Once enough salt is added to this tank the alarm will sound and a message will be transmitted over UART signaling an operator to manually reset the system. All functions of the system will be disabled at this time. 

*Obtaining the components, this project can also be tested in a different setting. However, we don't recommend testing this project to anyone who doesn't have full/complete information about this project.*

## Video Presentation of The Completed Project: 
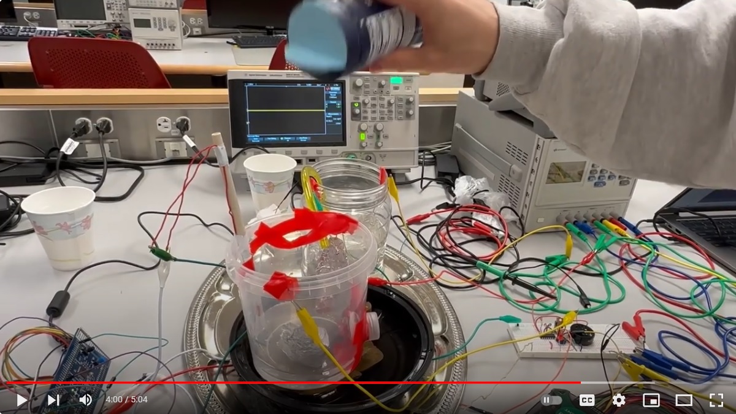
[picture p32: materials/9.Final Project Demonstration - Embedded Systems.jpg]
Final Project Demonstration (https://youtu.be/beLorS1tq-g)

### Behind The Scenes: 

#### 1.Behind the scenes:
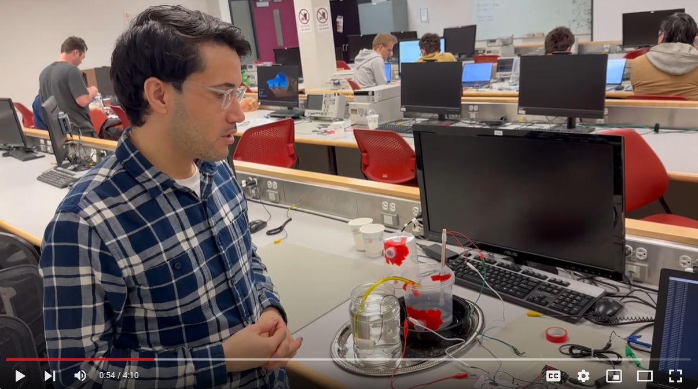
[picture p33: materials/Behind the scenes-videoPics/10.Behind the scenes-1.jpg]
1.Behind the scenes (https://youtu.be/_E30sTxkhJc)

#### 2.Behind the scenes:
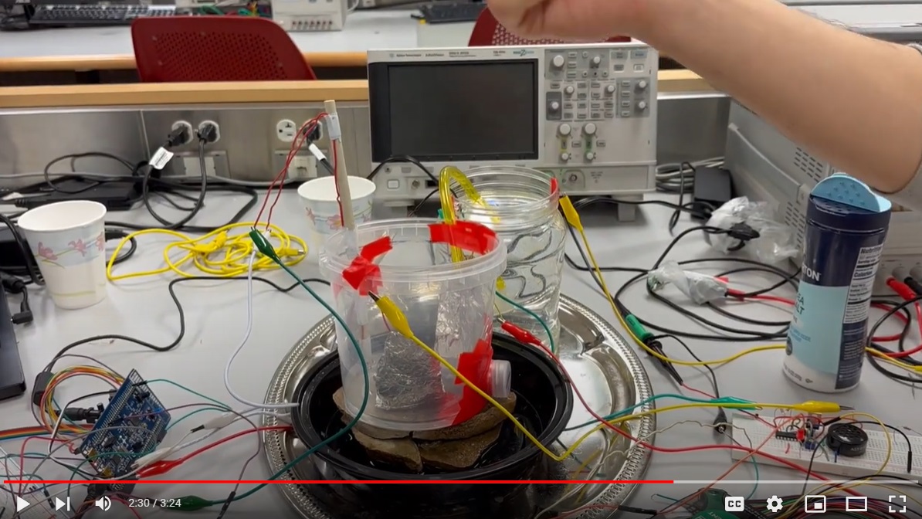
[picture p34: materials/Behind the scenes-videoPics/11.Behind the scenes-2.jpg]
2.Behind the scenes (https://youtu.be/jAEO7KFEs-s)

#### 3.Behind the scenes:
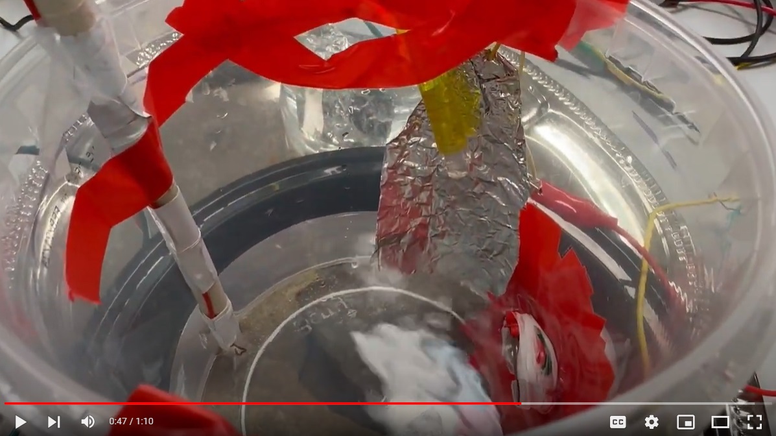
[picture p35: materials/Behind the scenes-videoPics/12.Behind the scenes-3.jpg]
3.Behind the scenes (https://youtu.be/mo8mnAZpZGU)

#### 4.Behind the scenes:
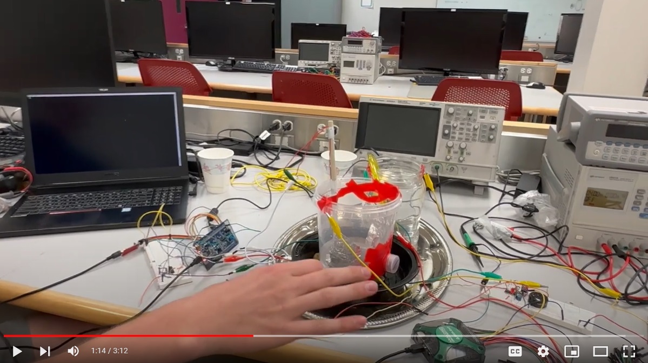
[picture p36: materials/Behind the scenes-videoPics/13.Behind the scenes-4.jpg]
4.Behind the scenes (https://youtu.be/cTMJ8XVg88U)

#### 5.Behind the scenes:
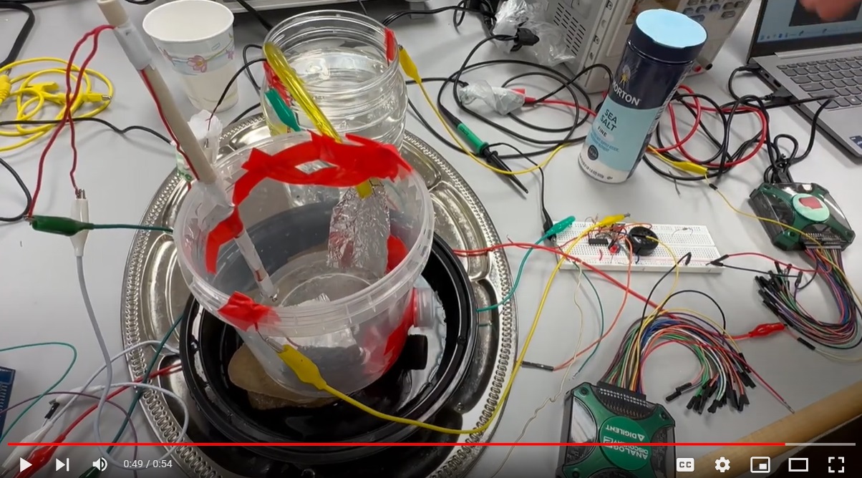
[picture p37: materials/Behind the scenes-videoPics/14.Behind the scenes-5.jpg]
5.Behind the scenes (https://youtu.be/9Yy0rnygG_Y)


#### Water Safity Testing:
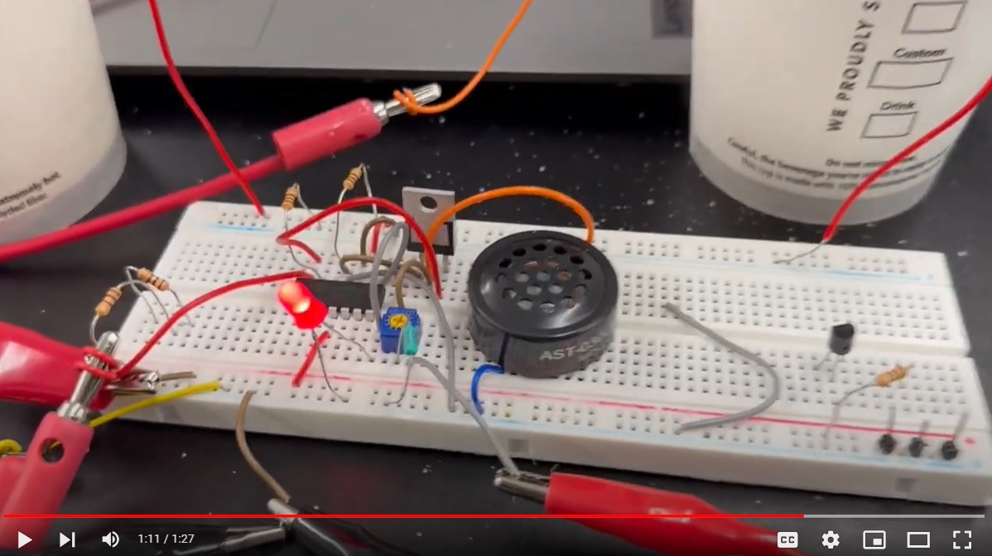
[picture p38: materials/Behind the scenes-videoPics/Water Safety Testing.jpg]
Water Safity Testing (https://youtu.be/uQ_QnTD59tI)


# Credits
- Thang Tran, Department of Chemical Engineering, The University of Utah:
	*- Thank you for your support on providing supplies in our experiments!*

- Ashton Snelgrove, Department of Electrical and Computer Engineering, The University of Utah:
	*- Thank you for your continuous support until the end of the semester!*

# Caution/Warnings

* Don't use any electric component that exceeds 5V.
* Don't use any metal with a wet hand and touch an electric component.
* Wash your hands after each experiment.
* Don't drink the water used for the testing/experiment.
* Make sure you check and be familiar with the op-amp and transistor's type and physics before starting the experiment.

# Examples of Good Software Practice (GSP)
<pre><ins>DRY</ins> :</pre>
DRY is an abbreviation of "Don't repeat yourself". It's a principle of Software Engineering that
has the goal of reducing repetition and redundancy in the coding. Using abstractions and normalization
are advised over redundancy <a href="https://en.wikipedia.org/wiki/Don%27t_repeat_yourself">[2]</a>.

<pre><ins>Separation of Concerns</ins> :</pre>
This concept is similar to the "divide and conquer" principle where you divide
a big software project into small projects to complete. A software design technique that focuses on separating 
and freeing functionalities of a program is called Modular programming. Making each of the divided small 
projects independent and addressing a separate concern, it'll make it easy to reduce, detect 
and fix the errors. <a href="https://en.wikipedia.org/wiki/Separation_of_concerns">[3]</a>

<pre><ins>Good Code Typing Practices</ins> :</pre>
Good coding practices can be listed as: Naming variables with a relevant name, commenting 
in between code lines with a brief explanation if the code is not self-explanatory, creating 
helper methods that can be used multiple times and by other sections.

<pre><ins>Testing Strategies</ins> :</pre>
Unit Testing can be summarized in 3 types of techniques:<br>

1. <ins>Black Box Testing : </ins> In this testing, input, user interface, and output parts are covered.
2. <ins>White Box Testing : </ins> In this testing, functionality, design structure, and code models are covered.
3. <ins>Gray Box Testing : </ins> In this testing, analysis of code performance, relevant test cases,
methods, and functions are covered.<a href="https://www.geeksforgeeks.org/unit-testing-software-testing/">[4]</a>

# References:
1. Canvas Page Class Materials.(For example, lecture slides, additional resources and pdf files). <br>
2. https://en.wikipedia.org/wiki/Don%27t_repeat_yourself<br>
3. https://en.wikipedia.org/wiki/Separation_of_concerns<br>
4. https://www.geeksforgeeks.org/unit-testing-software-testing/<br>

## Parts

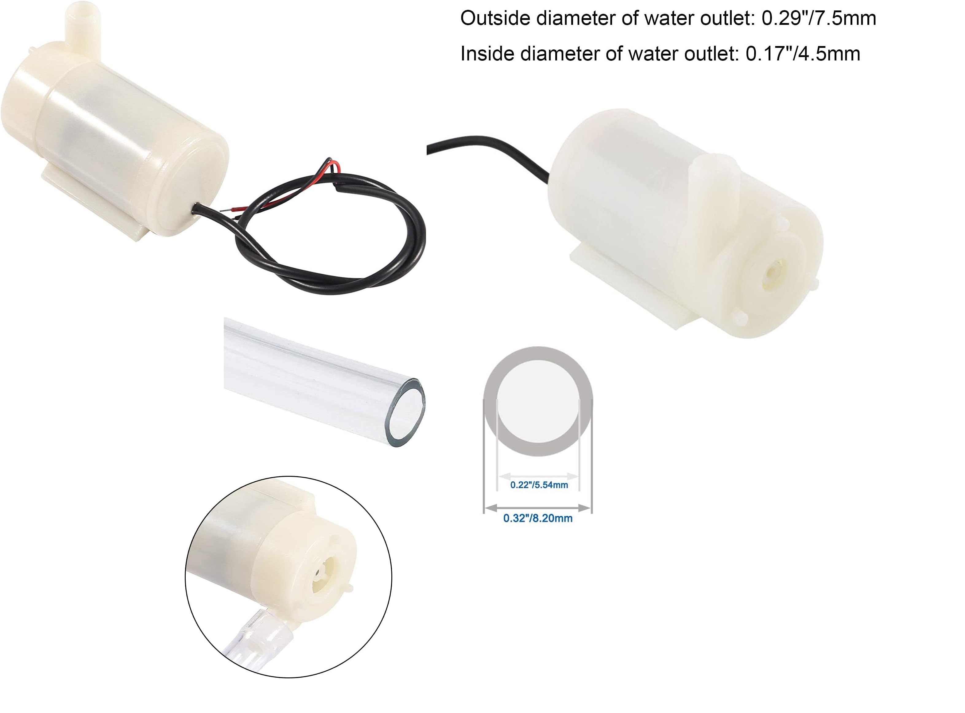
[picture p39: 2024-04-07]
materials/2.water pump.jpg

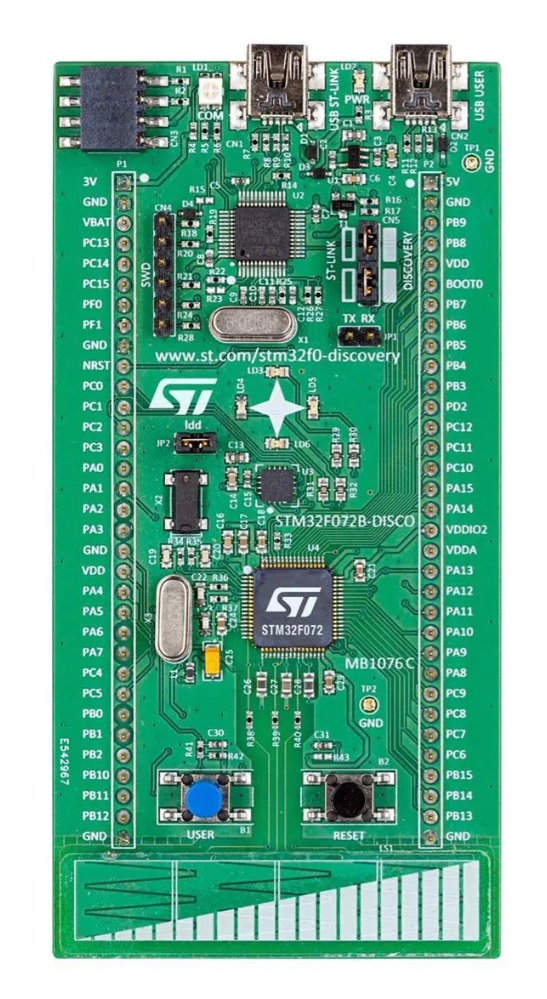
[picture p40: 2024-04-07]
materials/3.Microcontroller_STM32F072B-DISCO.jpg

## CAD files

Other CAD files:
materials/AutodeskFusionFiles/ECE6780_Final_project_schematic v1 v1.f3z

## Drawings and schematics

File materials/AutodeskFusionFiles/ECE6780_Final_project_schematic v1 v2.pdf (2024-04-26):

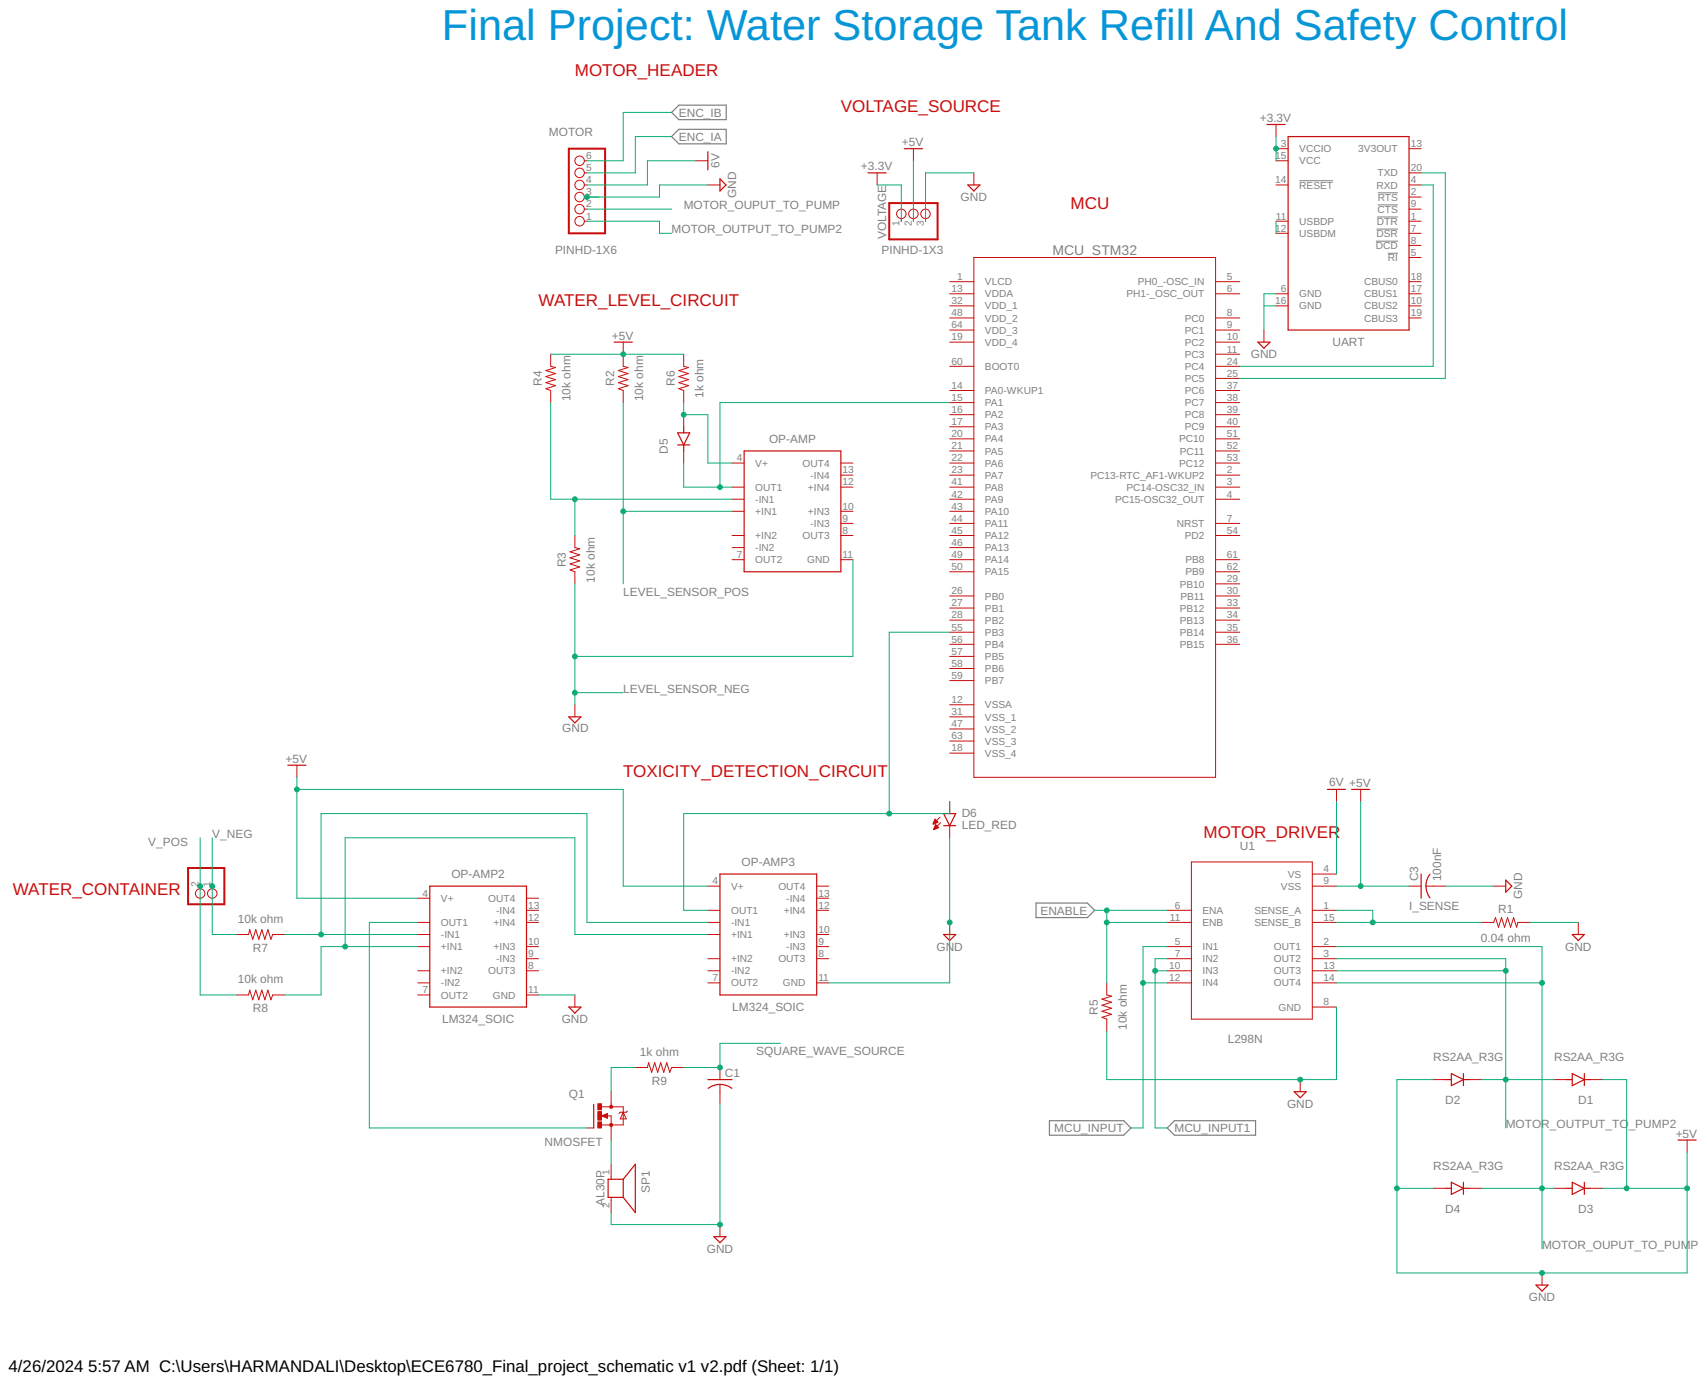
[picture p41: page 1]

Final Project: Water Storage Tank Refill And Safety Control

4/26/2024 5:57 AM C:\Users\HARMANDALI\Desktop\ECE6780_Final_project_schematic v1 v2.pdf (Sheet: 1/1)

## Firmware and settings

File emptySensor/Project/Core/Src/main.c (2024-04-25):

#include <stdio.h>
#include <stdlib.h>
#include "stm32f0xx.h"
#include "motor.h"

/* -------------------------------------------------------------------------------------------------------------
 *  Final Project Code - Water level controller and toxicity sensor 
 *  -------------------------------------------------------------------------------------------------------------
 */
volatile uint32_t debouncer;

void tranchar(char key);

void transtring(char key[]);

void Parse();

volatile int readData;
volatile int flagSet;
volatile int counter = 0;
volatile char color;
volatile int mode;

char errorstring[] = {'E','R','R','O','R',':','\t','I','N','V','A','L','I','D','\t','K','E','Y','\n','\0'}; 
char one[] = {'T','a','n','k',' ','E','m','p','t','y',',',' ','f','i','l','l','i','n','g',' ','i','n',' ','p','r','o','g','r','e','s','s','\n','\0'};
char done[] = {'F','i','l','l','i','n','g',' ','i','s',' ','c','o','m','p','l','e','t','e','!','\n','\0'};	
char errorstring2[] = {'T','O','X','I','C',' ','W','A','T','E','R','\t','M','A','N','U','A','L',' ','R','E','S','E','T',' ','R','E','Q','U','I','R','E','D','\n','\0'}; 
char cmdprompt[] = {'C','M','D','?','\0'};

char char1[] = {' ','M','o','d','e','\n','\0'};
char char2[] = {' ','S','e','t','t','i','n','g','\n','\0'};


/* -------------------------------------------------------------------------------------------------------------
 *  Miscellaneous Core Functions
 *  -------------------------------------------------------------------------------------------------------------
 */

void LED_init(void) {
    // Initialize PC8 and PC9 for LED's
    RCC->AHBENR |= RCC_AHBENR_GPIOCEN;                                          // Enable peripheral clock to GPIOC
    GPIOC->MODER |= GPIO_MODER_MODER8_0 | GPIO_MODER_MODER9_0 | GPIO_MODER_MODER6_0 | GPIO_MODER_MODER7_0;                  // Set PC8 & PC9 to outputs
    GPIOC->OTYPER &= ~(GPIO_MODER_MODER8_0 | GPIO_MODER_MODER9_0 | GPIO_MODER_MODER6_0 | GPIO_MODER_MODER7_0);                    // Set to push-pull output type
    GPIOC->OSPEEDR &= ~((GPIO_MODER_MODER8_0 | GPIO_MODER_MODER9_0 | GPIO_MODER_MODER6_0 | GPIO_MODER_MODER7_0) |
                        (GPIO_MODER_MODER8_0 | GPIO_MODER_MODER9_0 | GPIO_MODER_MODER6_0 | GPIO_MODER_MODER7_0));   // Set to low speed
    GPIOC->PUPDR &= ~((GPIO_MODER_MODER8_0 | GPIO_MODER_MODER9_0 | GPIO_MODER_MODER6_0 | GPIO_MODER_MODER7_0 | GPIO_PUPDR_PUPDR8_1) |
                      (GPIO_MODER_MODER8_0 | GPIO_MODER_MODER9_0 | GPIO_MODER_MODER6_0 | GPIO_MODER_MODER7_0));             // Set to no pull-up/down
    GPIOC->ODR &= ~(GPIO_MODER_MODER8_0 | GPIO_MODER_MODER9_0 | GPIO_MODER_MODER6_0 | GPIO_MODER_MODER7_0);                                   // Shut off LED's
}

void  button_init(void) {
    // Initialize PA0 for button input
    RCC->AHBENR |= RCC_AHBENR_GPIOAEN;                                          // Enable peripheral clock to GPIOA
    GPIOA->MODER &= ~(GPIO_MODER_MODER0_0 | GPIO_MODER_MODER0_1);               // Set PA0 to input
    GPIOC->OSPEEDR &= ~(GPIO_OSPEEDR_OSPEEDR0_0 | GPIO_OSPEEDR_OSPEEDR0_1);     // Set to low speed
    GPIOC->PUPDR |= GPIO_PUPDR_PUPDR0_1;                                        // Set to pull-down
}

//Initialize low level sensor cutoff trigger
void exti_init(void)	{
	
	//Configure user pushbutton for low water level sensor interrupt
		RCC->AHBENR |= (1<<17); //GPIOA enable
		RCC->AHBENR |= (1<<18);	//GPIOB enable
	
		GPIOA->MODER &= ~((1<<0) | (1<<1));
		GPIOA->OTYPER &= 0;
		GPIOA->OSPEEDR &= 0;
		GPIOA->PUPDR |= 2;
	
		GPIOB->MODER &= ~((1<<6) | (1<<7));
		GPIOB->OTYPER &= 0;
		GPIOB->OSPEEDR &= 0;
		GPIOB->PUPDR |= (2<<6);
	//GPIOB->PUPDR |= (2<<6);
		
		EXTI->IMR |= (1<<3); //PA3

		//Unmask interrupt generation on EXTI input.
		EXTI->IMR |= 1; //PA0
		
	
		//Set input to have a rising-edge trigger.
		EXTI->RTSR |= 1; //PA0
		EXTI->RTSR |= (1<<3); //PB3

	
		//Enable the SYSCFG Peripheral and enable PA0
		RCC->APB2ENR |= 1;
	
		SYSCFG->EXTICR[0] &= 0;	//EXTI0
		
		SYSCFG->EXTICR[0] |= (1<<12);	//EXTI3
		
		//Set priority of external interrupts, shut down being highest priority
		__NVIC_EnableIRQ(EXTI0_1_IRQn);
		__NVIC_EnableIRQ(EXTI2_3_IRQn);
	
		NVIC_SetPriority(SysTick_IRQn, 3);
	
		//Low water level interrupt on PA0
		NVIC_SetPriority(EXTI0_1_IRQn, 1);
		
		//Toxic water interrupt on PB3
		NVIC_SetPriority(EXTI2_3_IRQn, 2);
	
}

void usart_init(void)		{
	GPIOC->MODER |= (10 << 8);
	
	//Enable afrl for pc4 and pc5 
	// 00010001 shifted left 16 (AF1) (AF1)
	GPIOC->AFR[0] |= (17 << 16); 
	
	//Enable the clock to the USART register. 
	//Writes a 1 to enable USART3 Clock
	RCC->APB1ENR |= (1 << 18);
	
	//Set the baud rate BRR value
	USART3->BRR = 69; //69(HAL_RCC_GetHCLKFreq()/115200)
	
	//Enable transmit and recieve as well as enable the USART
	USART3->CR1 |= 13;
	
	//Enable RXNE Interrupt
	USART3->CR1 |= (1<<5);
	
	//Interrupt enable 
	__NVIC_EnableIRQ(USART3_4_IRQn);
	NVIC_SetPriority(USART3_4_IRQn, 0);
	
}

/* Called by SysTick Interrupt
 * Performs button debouncing, changes wave type on button rising edge
 * Updates frequency output from ADC value
 */
void HAL_SYSTICK_Callback(void) {
    // Remember that this function is called by the SysTick interrupt

    debouncer = (debouncer << 1);
    if(GPIOA->IDR & (1 << 0)) {
        debouncer |= 0x1;
    }

    if(debouncer == 0x7FFFFFFF) {
    switch(target_rpm) {
        case 80:
            target_rpm = 50;
            break;
        case 50:
            target_rpm = 81;
            break;
        case 0:
            target_rpm = 80;
            break;
        default:
            target_rpm = 0;
            break;
        }
    }
}

/* -------------------------------------------------------------------------------------------------------------
 * Main Program Code
 *
 * Starts initialization of peripherals
 * Begins main program loop
 * -------------------------------------------------------------------------------------------------------------
 */
volatile uint32_t encoder_count = 0;
volatile uint32_t PWM = 0;
volatile uint32_t PWMcap = 100;
volatile uint32_t interruptCount = 0;
volatile uint8_t levelflag = 0;
volatile uint32_t toxicflag = 0;
volatile uint32_t count= 0;

int main(int argc, char* argv[]) {

    debouncer = 0;                          
		HAL_Init();															// Initialize HAL
    LED_init();                             // Initialize LED's
    button_init();                          // Initialize button
    motor_init();                           // Initialize motor code
	
		exti_init();
		usart_init();
		
	
	
	
    while (1) {
			
			//Check for toxic flag interrupt
			GPIOC->BSRR |= (1<<9);
			
			if(toxicflag > 0){
				transtring(errorstring2);
				break;
			}
			else if(toxicflag == 0){
			
				if(flagSet == 1){
			
					Parse();
				
					flagSet = 0;
			
				}
				
				pwm_setDutyCycle(PWM);
				
				// If low level sensor triggers an interrupt, set the pump to fill container
				if(levelflag > 0){
					
					transtring(one); // Message pump is running
					GPIOC->BSRR |= (1<<8);
					
					//Sets water level and runs pump 
					while(count < 2000000){
						
						pwm_setDutyCycle(PWM);
				
						if(toxicflag > 0){
						transtring(errorstring2);
						PWM=0;
						break;
						}
						count++;
					}
					
					GPIOC->BSRR |= (1<<24);
					
					transtring(done);
					count = 0;
					PWM = 0;
					levelflag = 0;
				}
			
    }
		
		
	}
}

//Function to read USART commands
void Parse(void){
	
	if(counter == 0){
		color = readData;
		
		if(!(color == 'a'|| color == 'm')){
			transtring(errorstring);
			counter = 0;
		}
		else{
			transtring(char1);
			counter++;
		}
	}
	else if(counter == 1){
		mode = readData;
		transtring(char2);
		counter++;
		
	}
	
	//Used to set motor rates
	if(counter == 2){
		if(color == 'a'){
			if(mode == '0'){
		
				PWMcap = 90;
			}
			else if(mode == '1'){
				
				PWMcap = 95;
			}
			else if(mode == '2'){
			
				PWMcap = 100;
			}
			else
				transtring(errorstring);
			
		}
		//Used to turn pump on and off manually 
		else if(color == 'm'){
			if(mode == '0'){
				PWM = 0;
			}
			else if(mode == '1'){
				PWM = PWMcap;
			}
			else
				transtring(errorstring);
			
			
		}
		//Error message if invalid color is entered
		else if(color != 13 || color != 'a' || color != 'm')  {
			transtring(errorstring);
		}
		counter = 0;
	}
		
	
}
	
//USART3 Interrupt handler
void USART3_4_IRQHandler(void){
	
	if (USART3->ISR & USART_ISR_RXNE){
	//transtring(testpoint);
		flagSet = 1;
		
		readData = USART3->RDR;
		//transtring(testpoint);
	}
	
}
// Function used to transmit a character
// Takes a single character parameter and saves that into the TDR register.
void tranchar(char key)
{
	//While the transmit data register is not empty...
	// USART3->ISR != (USART3->ISR &= USART_ISR_TXE_Msk) 
	while(!(USART3->ISR & USART_ISR_TXE))
	{
		
	}
	
	USART3->TDR = key;
}

//Function used to transmit a string of chars
//Takes an array of chars and transmits each char seperately. 
void transtring(char key[])
{
	
		char current = key[0];
		
		for(int i = 0; current != 0; i++)
		{
			current = key[i];
			tranchar(current);
		}
}

//Handler to interrupt main when the water level drops below a set threshold. 
void EXTI0_1_IRQHandler(void){

	static int check = 0; // Static variable to keep track of LED state
	if(interruptCount == 0){
		levelflag = 1;
	  PWM = PWMcap;
		GPIOC->BSRR |= (1<<7); // blue LED signals pump is running
		
		interruptCount++;
		
	}
	else if(interruptCount == 1){
		PWM = 0;
		GPIOC->BSRR |= (1<<23); // turn LED signal off
		interruptCount = 0;
	}
	// Toggle between green and orange LEDs
		
		EXTI->PR |= 1;
}

//Toxic water interrupt
void EXTI2_3_IRQHandler(void){

	
		//If the pump is not running and toxic water is detected, stop system
		if(levelflag != 1){
			pwm_setDutyCycle(0);
			PWM = 0;
			GPIOC->BSRR |= (1<<6);
			toxicflag = 1;
			//Dont exit interrupt, user reset is now required.
		}
		EXTI->PR |= 1;
}

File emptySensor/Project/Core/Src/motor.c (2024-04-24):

/* -------------------------------------------------------------------------------------------------------------
 *  Motor Control and Initialization Functions
 * -------------------------------------------------------------------------------------------------------------
 */
#include "motor.h"

volatile int16_t error_integral = 0;    // Integrated error signal
volatile uint8_t duty_cycle = 0;    	// Output PWM duty cycle
volatile int16_t target_rpm = 0;    	// Desired speed target
volatile int16_t motor_speed = 0;   	// Measured motor speed
volatile int8_t adc_value = 0;      	// ADC measured motor current
volatile int16_t error = 0;         	// Speed error signal
volatile uint8_t Kp = 1;            	// Proportional gain
volatile uint8_t Ki = 1;            	// Integral gain
volatile uint8_t output = 0;   
// Sets up the entire motor drive system
void motor_init(void) {
    pwm_init();
    encoder_init();
    ADC_init();
}

// Sets up the PWM and direction signals to drive the H-Bridge
void pwm_init(void) {
    
    // Set up pin PA4 for H-bridge PWM output (TIMER 14 CH1)
    GPIOA->MODER |= (1 << 9);
    GPIOA->MODER &= ~(1 << 8);

    // Set PA4 to AF4,
    GPIOA->AFR[0] &= 0xFFF0FFFF; // clear PA4 bits,
    GPIOA->AFR[0] |= (1 << 18);

    // Set up a PA5, PA6 as GPIO output pins for motor direction control
    GPIOA->MODER &= 0xFFFFC3FF; // clear PA5, PA6 bits,
    GPIOA->MODER |= (1 << 10) | (1 << 12);
    
    //Initialize one direction pin to high, the other low
    GPIOA->ODR |= (1 << 5);
    GPIOA->ODR &= ~(1 << 6);

    // Set up PWM timer
    RCC->APB1ENR |= RCC_APB1ENR_TIM14EN;
    TIM14->CR1 = 0;                         // Clear control registers
    TIM14->CCMR1 = 0;                       // (prevents having to manually clear bits)
    TIM14->CCER = 0;

    // Set output-compare CH1 to PWM1 mode and enable CCR1 preload buffer
    TIM14->CCMR1 |= (TIM_CCMR1_OC1M_2 | TIM_CCMR1_OC1M_1 | TIM_CCMR1_OC1PE);
    TIM14->CCER |= TIM_CCER_CC1E;           // Enable capture-compare channel 1
    TIM14->PSC = 1;                         // Run timer on 24Mhz
    TIM14->ARR = 1200;                      // PWM at 20kHz
    TIM14->CCR1 = 0;                        // Start PWM at 0% duty cycle
    
    TIM14->CR1 |= TIM_CR1_CEN;              // Enable timer
}

// Set the duty cycle of the PWM, accepts (0-100)
void pwm_setDutyCycle(uint8_t duty) {
    if(duty <= 100) {
        TIM14->CCR1 = ((uint32_t)duty*TIM14->ARR)/100;  // Use linear transform to produce CCR1 value
        // (CCR1 == "pulse" parameter in PWM struct used by peripheral library)
			
    }
		
}

// Sets up encoder interface to read motor speed
void encoder_init(void) {
    
    // Set up encoder input pins (TIMER 3 CH1 and CH2)
    RCC->AHBENR |= RCC_AHBENR_GPIOBEN;

		//UNCOMMENT THESE TEST
    //GPIOB->MODER &= ~(GPIO_MODER_MODER4_0 | GPIO_MODER_MODER5_0);
    //GPIOB->MODER |= (GPIO_MODER_MODER4_1 | GPIO_MODER_MODER5_1);
    //GPIOB->AFR[0] |= ( (1 << 16) | (1 << 20) );

    // Set up encoder interface (TIM3 encoder input mode)
    RCC->APB1ENR |= RCC_APB1ENR_TIM3EN;
    TIM3->CCMR1 = 0;
    TIM3->CCER = 0;
    TIM3->SMCR = 0;
    TIM3->CR1 = 0;

    TIM3->CCMR1 |= (TIM_CCMR1_CC1S_0 | TIM_CCMR1_CC2S_0);   // TI1FP1 and TI2FP2 signals connected to CH1 and CH2
    TIM3->SMCR |= (TIM_SMCR_SMS_1 | TIM_SMCR_SMS_0);        // Capture encoder on both rising and falling edges
    TIM3->ARR = 0xFFFF;                                     // Set ARR to top of timer (longest possible period)
    TIM3->CNT = 0x7FFF;                                     // Bias at midpoint to allow for negative rotation
    // (Could also cast unsigned register to signed number to get negative numbers if it rotates backwards past zero
    //  just another option, the mid-bias is a bit simpler to understand though.)
    TIM3->CR1 |= TIM_CR1_CEN;                               // Enable timer

    // Configure a second timer (TIM6) to fire an ISR on update event
    // Used to periodically check and update speed variable
    RCC->APB1ENR |= RCC_APB1ENR_TIM6EN;
    
    // Select PSC and ARR values that give an appropriate interrupt rate
    TIM6->PSC = 11;
    TIM6->ARR = 30000;
    
    TIM6->DIER |= TIM_DIER_UIE;             // Enable update event interrupt
    TIM6->CR1 |= TIM_CR1_CEN;               // Enable Timer

    NVIC_EnableIRQ(TIM6_DAC_IRQn);          // Enable interrupt in NVIC
    NVIC_SetPriority(TIM6_DAC_IRQn,2);
}
// Encoder interrupt to calculate motor speed, also manages PI controller
void TIM6_DAC_IRQHandler(void) {
    /* Calculate the motor speed in raw encoder counts
     * Note the motor speed is signed! Motor can be run in reverse.
     * Speed is measured by how far the counter moved from center point
     */
    motor_speed = (TIM3->CNT - 0x7FFF);
    TIM3->CNT = 0x7FFF; // Reset back to center point
    
    // Call the PI update function
    PI_update();

    TIM6->SR &= ~TIM_SR_UIF;        // Acknowledge the interrupt
}

void ADC_init(void) {

    // Configure PA1 for ADC input (used for current monitoring)
    GPIOA->MODER |= (GPIO_MODER_MODER1_0 | GPIO_MODER_MODER1_1);

    // Configure ADC to 8-bit continuous-run mode, (asynchronous clock mode)
    RCC->APB2ENR |= RCC_APB2ENR_ADCEN;

    ADC1->CFGR1 = 0;                        // Default resolution is 12-bit (RES[1:0] = 00 --> 12-bit)
    ADC1->CFGR1 |= ADC_CFGR1_CONT;          // Set to continuous mode
    ADC1->CHSELR |= ADC_CHSELR_CHSEL1;      // Enable channel 1

    ADC1->CR = 0;
    ADC1->CR |= ADC_CR_ADCAL;               // Perform self calibration
    while(ADC1->CR & ADC_CR_ADCAL);         // Delay until calibration is complete

    ADC1->CR |= ADC_CR_ADEN;                // Enable ADC
    while(!(ADC1->ISR & ADC_ISR_ADRDY));    // Wait until ADC ready
    ADC1->CR |= ADC_CR_ADSTART;             // Signal conversion start
}
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

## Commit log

2024-04-05 Project for microcontroller motor/sensor implementation
    Base code for system implementation, 2/5/24.
2024-04-07 Delete Project/Sample Code/Lab02/Drivers/CMSIS/NN/NN_Lib_Tests/nn_test/Ref_Implementations/arm_depthwise_separable_conv_HWC_q7_ref_nonsquare.c
    This file causes an error when pulling from the repo. It says the file name is too long.
2024-04-07 Delete Project/Sample Code/Lab02/Drivers/CMSIS/NN/NN_Lib_Tests/nn_test/Ref_Implementations/arm_fully_connected_mat_q7_vec_q15_opt_ref.c
    "This file causes an error when pulling from the repo. It says the file name is too long"
2024-04-08 LTSpice simulation for water level sensor
2024-04-12 Milestone 3 code
    functional failsafe to shut off water pump.
    [main.c]
2024-04-12 Update to milestone
    Adds USART control to motor
2024-04-14 Delete materials/1stExpPics/desktop.ini. No need.
    No need for this file.
2024-04-14 Water Empty/Level Sensor Files Are Combined.
    All water level/empty sensor related project files are organized here.
2024-04-14 Water Safety files are here.
    All Water Safety sensor related files are organized here.
2024-04-14 LtSpice files for the Water Safety Sensor.
    Draft of the LTSpice files for the water safety sensor.
2024-04-18 Custom-made motor driver.
2024-04-18 USB/UART Serial converter based on FTDI FT232RL
2024-04-22 Multiple interrupts added to final code.
2024-04-25 Addition of schematic photo
2024-04-25 Motor driver photo added to readme
2024-04-25 Additional drawn schematics added to readme
2024-04-26 Added Project Schematic files
    [ECE6780_Final_project_schematic v1.f3z]
2024-04-26 Safety sensor circuit and test set-up picture.
2024-04-26 Schematic is added: Auto fusion program drawing and a picture copy.
    [ECE6780_Final_project_schematic v1 v1.f3z, ECE6780_Final_project_schematic v1.f3z]
2024-04-26 Schematic is updated.
2024-04-26 Add the Schematic screenshot.
2024-04-26 The picture of the Schematic is added.
